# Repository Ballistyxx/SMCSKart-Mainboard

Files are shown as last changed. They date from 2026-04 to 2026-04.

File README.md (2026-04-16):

# SMCSKart Mainboard

Custom PCB integrating every system in the SMCS Robotics 8th period go-kart. The board acts as the central hub between a Raspberry Pi 4, a Teensy 4.1, all motor controller I/O, sensors, and peripherals.

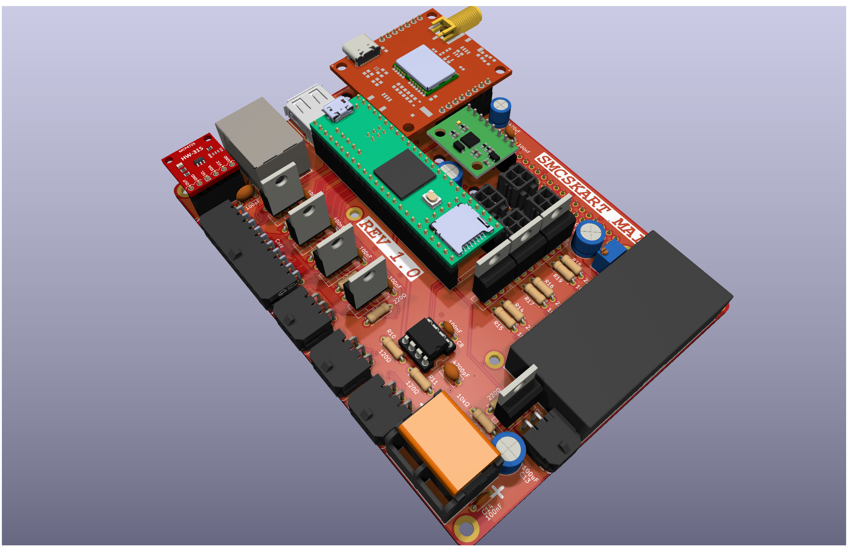
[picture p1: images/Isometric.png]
Isometric View of the SMCSKart PCB


<div style="display: flex; justify-content: space-between;">
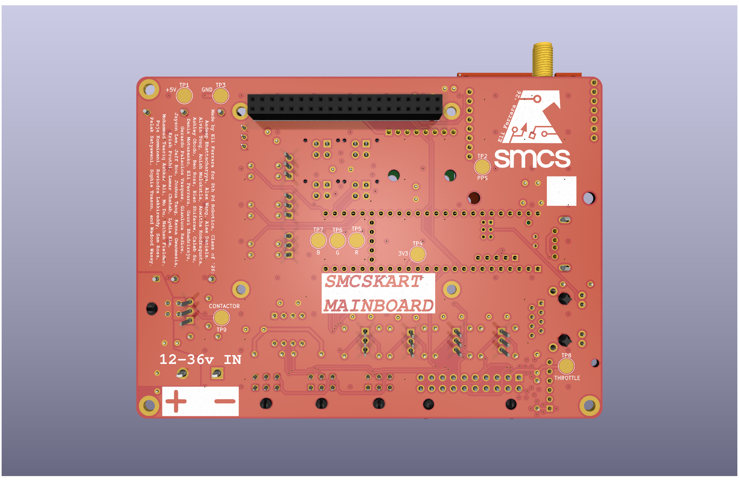
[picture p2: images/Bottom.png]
  
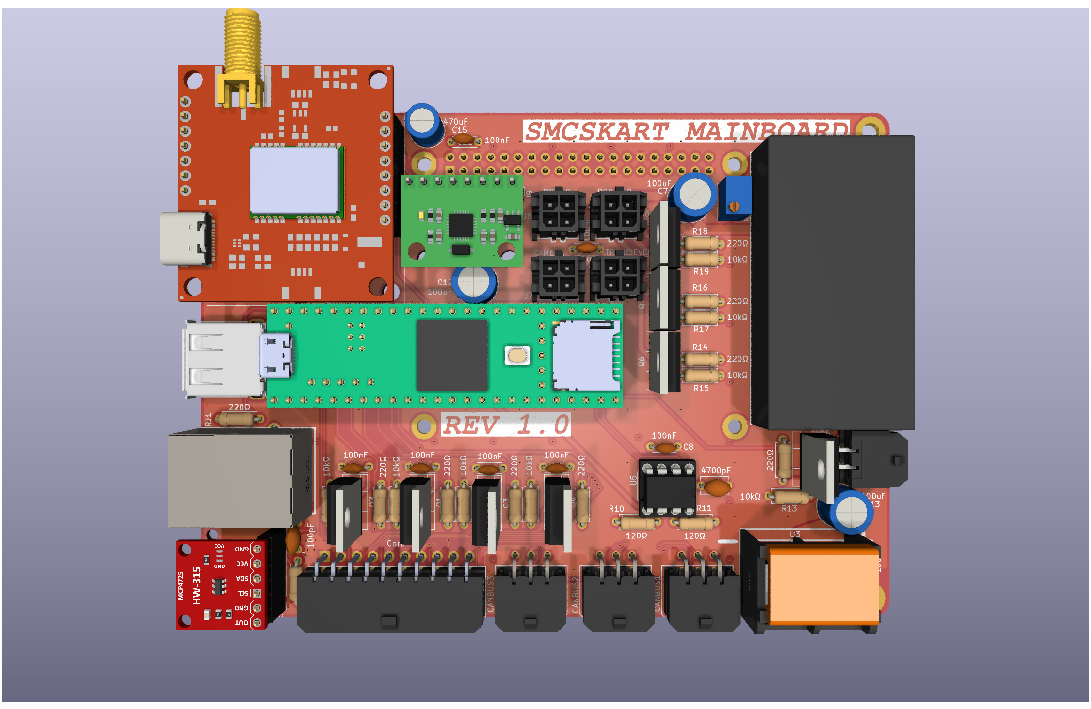
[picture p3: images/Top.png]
  
</div>

---

## Components

| Component | Description |
|---|---|
| Raspberry Pi 4 | Main compute; connected via 40-pin header |
| Teensy 4.1 | Real-time microcontroller with onboard Ethernet |
| NEO-M9N | GPS module (connected to Pi I2C + PPS to Teensy) |
| MPU6050 | 6-axis accelerometer/gyroscope (connected to Pi I2C) |
| MCP4725 | 12-bit DAC for throttle signal generation (connected to Teensy I2C) |
| MCP2562-E/P | CAN bus transceiver |
| IRLZ44N | Logic-level N-channel MOSFETs for all toggle/switch outputs (with pulldown resistors) |
| ND721000 | FarDriver BLDC/PMSM speed controller (RS232 interface) |

---

## Power Rails

The board supplies three voltage rails available on the extra power port:

| Rail | Voltage |
|---|---|
| 3V3 | 3.3 V |
| 5V | 5 V |
| 24V | 24 V (also used for LED strip) |

---

## Teensy 4.1 Pin Assignments

### Serial / UART

| Pin(s) | Interface | Connected To | Notes |
|---|---|---|---|
| 0, 1 | Serial1 (TX, RX) | ND721000 ESC | RS232 level — programming/telemetry port on ESC |
| 7, 8 | Serial2 (TX, RX) | Raspberry Pi 4 | UART bridge between Teensy and Pi |
| 14, 15 | Serial3 (TX, RX) | Transceiver module | RF/wireless transceiver comms |
| 34, 35 | Serial8 (TX, RX) | FPV camera | UART control for FPV camera |

### I2C

| Pin(s) | Bus | Connected To |
|---|-----|---|
| 18, 19 | SDA, SCL | MCP4725 DAC (throttle control) |

### CAN Bus

| Pin(s) | Signal | Notes |
|---|---|---|
| 30, 31 | CRX, CTX | Via MCP2562-E/P transceiver; 120 Ω termination required at each end |

### Digital I/O — ESC Control & Sensors

All toggle output pins drive an IRLZ44N MOSFET with a pulldown resistor, providing an active-low ground signal to the ESC connector.

| Pin | Function | ESC Signal | Direction |
|-----|---|---|---|
| 2 | Hall Pulses input | Hall Pulses (ESC pin 18) | Input from ESC |
| 3 | Reverse toggle | REV (ESC pin 8) | Output to ESC |
| 4 | Brake toggle | Low Brake (ESC pin 21) | Output to ESC |
| 5 | High speed toggle | High Speed (ESC pin 3) | Output to ESC |
| 6 | Low speed toggle | Low Speed (ESC pin 2) | Output to ESC |
| 9 | Cruise control | Cruise/Boost connector | Output to ESC |
| 10 | PPS | NEO-M9N GPS pulse-per-second | Input from GPS |
| 32 | Contactor toggle | Main contactor relay | Output |

### PWM — LED Strip (24 V)

| Pin | Channel |
|-----|---|
| 37 | Red |
| 36 | Green |
| 33 | Blue |

### Auxiliary (EX1–EX5)

| Pin | Label |
|-----|---|
| 25 | EX1 |
| 26 | EX2 |
| 27 | EX3 |
| 28 | EX4 |
| 29 | EX5 |

---

## Raspberry Pi 4 I2C Bus

| Device | Address | Function |
|---|---|---|
| NEO-M9N | — | GPS module |
| MPU6050 | 0x68 | Accelerometer / Gyroscope |

---

## ND721000 ESC Interface

The Teensy communicates with the ND721000 over **Serial1 (pins 0/1) at RS232 levels** (programming/telemetry port). In addition, discrete signals are routed between the board and the ESC's connector harness.

### ESC Connector Pin Reference

| ESC Pin | Color | Signal | Direction | Teensy Pin | Notes |
|---|---|---|---|---|---|
| 1 | Yellow | Hall A | → ESC | — | Motor hall sensor A |
| 2 | Blue-White | Low Speed | ← Teensy | 6 | Ground to activate low speed profile |
| 3 | Yellow-White | High Speed | ← Teensy | 5 | Ground to activate high speed profile |
| 4 | Red | HALL+ | — | — | ~14 V supply to hall sensors / encoder |
| 5 | Brown-Yellow | CAN L | ↔ | — | CAN bus low (optional; 120 Ω termination required) |
| 6 | Black | GND (Hall) | — | — | Hall sensor ground |
| 7 | Black | B− / GND | — | — | Battery negative / signal ground |
| 8 | Brown-White | REV | ← Teensy | 3 | Ground to request reverse direction |
| 9 | Purple | Speedometer signal | → | — | Analog speed output for speedometer gauge |
| 10 | Orange | Key | — | — | Main power-on input (connect to key switch via 5A fuse) |
| 11 | Gray | High Brake | ← Teensy | 4 | Active-high (12 V) brake input |
| 12 | Green | Hall B | → ESC | — | Motor hall sensor B |
| 13 | Light-Blue | SPD (digital speed pulse) | → | — | Square-wave RPM output for digital speedo / ECU |
| 14 | Black-White | FW (anti-theft) | ← | — | Ground to activate anti-theft lockout (error code 6) |
| 15 | Red-Yellow | CAN H | ↔ | — | CAN bus high (optional; 120 Ω termination required) |
| 16 | Black | GND (serial/switch) | — | — | Signal ground for serial and switch circuits |
| 17 | White | Hall P (encoder index) | → ESC | — | Once-per-revolution encoder reference pulse |
| 18 | Brown | Hall Pulses signal | → Teensy | 2 | Speed pulse output used as tachometer reference |
| 19 | Brown-Red | Lock Phase | — | — | Anti-theft motor phase lock wire |
| 20 | Orange | Key (anti-theft) | — | — | Secondary key input for anti-theft subsystem |
| 21 | Yellow-Green | Low Brake | ← Teensy | 4 | Active-low brake input; ground to signal braking |
| 22 | Blue | Hall C | → ESC | — | Motor hall sensor C |
| 23 | Brown-Blue | TxD (serial) | → Teensy | 0 (RX) | ESC serial transmit → Teensy Serial1 RX |
| 24 | White | Motor Temp | → ESC | — | Motor temperature sensor (PTC/NTC/KTY) |
| 25 | — | — | — | — | — |
| 26 | Black | GND (throttle/brake) | — | — | Shared signal ground for throttle and brake circuits |
| 27 | Green-White | TPS (throttle) | ← DAC | — | Throttle position signal (0.5–4.3 V); driven by MCP4725 |
| 28 | Red-White | ACC+ (5 V) | → throttle sensor | — | 5 V regulated supply for throttle sensor |
| 29 | Brown-Green | V+ (serial power) | → adapter | — | 5 V supply for USB-TTL programming adapter |
| 30 | Pink | B+ (anti-theft) | — | — | Always-live battery positive for anti-theft device |
| 31 | Brown-Red | RxD (serial) | ← Teensy | 1 (TX) | ESC serial receive ← Teensy Serial1 TX |

> **Note:** High Brake (pin 11) is active-high (12 V) while Low Brake (pin 21) is active-low (GND). Both can signal braking; the board uses pin 21 via MOSFET toggle (Teensy pin 4).
> **Note:** Medium speed mode is the ESC default when neither High Speed nor Low Speed is grounded.

---

## External Connectors / Ports

| Port | Description |
|---|---|
| 40-pin header | Raspberry Pi 4 HAT connector |
| USB-A | HID peripheral (keyboard, gamepad, etc.) |
| Ethernet | Networking (Teensy 4.1 native Ethernet) |
| CAN × 3 | CANBUS + I2C interface ports |
| Contactor | Trigger port for main contactor relay (Teensy pin 32) |
| FPV camera | UART port (Teensy Serial8, pins 34/35) |
| Transceiver | RF transceiver UART port (Teensy Serial3, pins 14/15) |
| Power port | Extra 3V3 / 5V / 24V supply breakout |
| LED strip | 24 V RGB PWM output (pins 37, 36, 33) |

For images of each port's annotated pinout, see [./docs/PINOUTS.md](./docs/PINOUTS.md)

Made by Eli Ferrara, SMCS Class of 2026
MIT License

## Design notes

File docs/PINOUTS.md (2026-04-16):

# GPIO Pinouts

<div align="center">
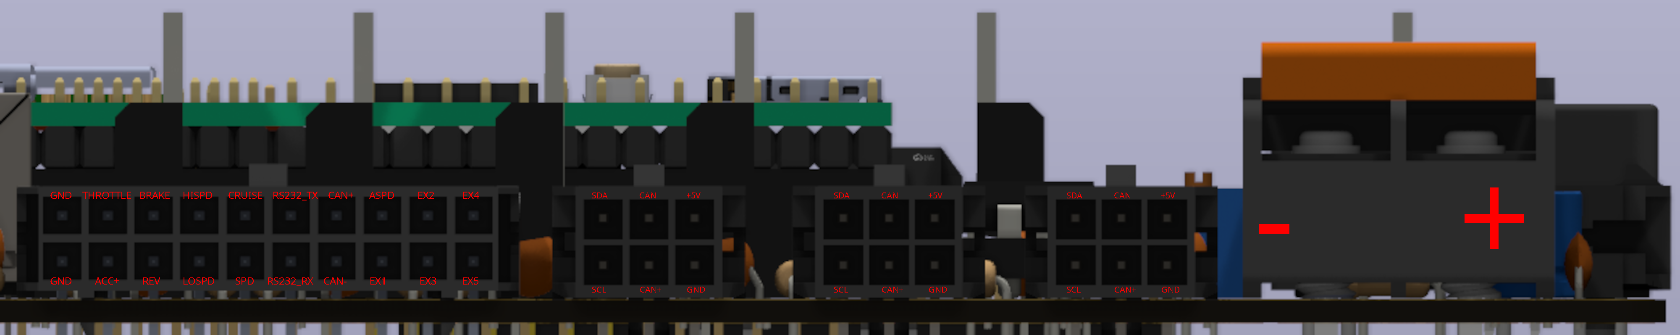
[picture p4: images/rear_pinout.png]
Rear Pinout
  
  <p><i>Rear view pinout diagram</i></p>
</div>

<div align="center">
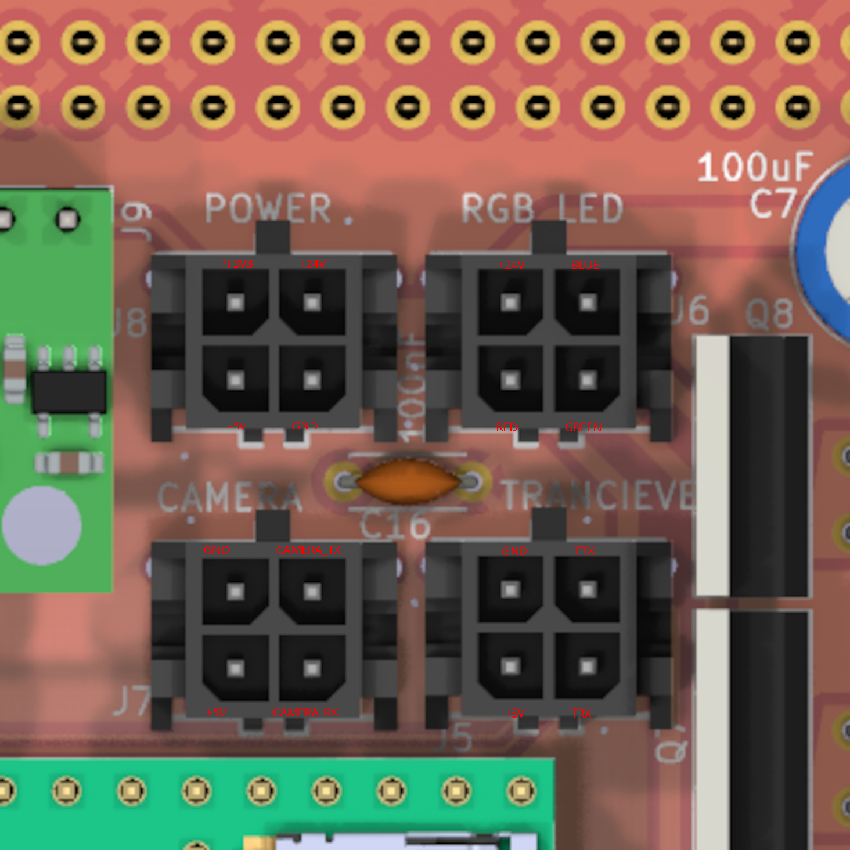
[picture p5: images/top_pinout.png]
Top Pinout
  
  <p><i>Top view pinout diagram; NOTE: TTX and TRX correspond to the tranciever's TX and RX, not the Teensy's TX and RX. Likewise, CAMERA_TX and CAMERA_RX correspond to the camera's TX and RX.</i></p>
</div>

<div align="center">
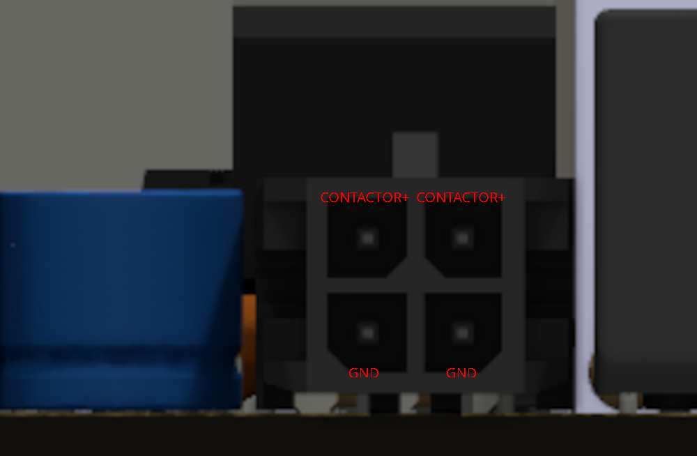
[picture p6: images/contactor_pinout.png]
Contactor Pinout
  
  <p><i>Contactor pinout diagram</i></p>
</div>

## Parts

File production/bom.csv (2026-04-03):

Designator | Footprint | Quantity | Value | LCSC Part #
C1, C10, C11, C14, C16, C3, C4, C5, C8 | C_Disc_D4.3mm_W1.9mm_P5.00mm | 9 | 100nF
C12, C13, C7, C9 | C_Radial_D8.0mm_H7.0mm_P3.50mm | 4 | 100uF
C15 | C_Radial_D6.3mm_H7.0mm_P2.50mm | 1 | 470uF
C2 | C_Disc_D6.0mm_W2.5mm_P5.00mm | 1 | 100pF
C6 | C_Disc_D5.1mm_W3.2mm_P5.00mm | 1 | 4700pF
CANBUS1, CANBUS2, CANBUS3 | Molex_Micro-Fit_3.0_43045-0600_2x03_P3.00mm_Horizontal | 3 | ZX-MX3_0-2-3PWZ | C7541602
J1 | PinSocket_2x20_P2.54mm_Vertical | 1 | Raspberry_Pi_4
J2 | CONN-TH_20P-P3.00_HC-MX3.0-2X10AW | 1 | Core
J3 | PinHeader_1x06_P2.54mm_Vertical | 1 | MCP4275_Breakout
J4 | CONN-TH_0430450400 | 1 | 0430450400 | C122413
J5 | CONN-TH_4P-P3.00_HC-MX3.0-2X2A | 1 | TRANCIEVER | C7541613
J6 | CONN-TH_4P-P3.00_HC-MX3.0-2X2A | 1 | RGB_LED | C7541613
J7 | CONN-TH_4P-P3.00_HC-MX3.0-2X2A | 1 | CAMERA | C7541613
J8 | CONN-TH_4P-P3.00_HC-MX3.0-2X2A | 1 | POWER | C7541613
J9 | PinHeader_1x08_P2.54mm_Vertical | 1 | MPU-6050_Breakout
Q1, Q2, Q3, Q4, Q5, Q6, Q7, Q8 | TO-220-3_Vertical | 8 | IRLZ44N
R1, R13, R15, R17, R19, R5, R8, R9 | R_Axial_DIN0207_L6.3mm_D2.5mm_P7.62mm_Horizontal | 8 | 10kΩ
R10, R11 | R_Axial_DIN0207_L6.3mm_D2.5mm_P7.62mm_Horizontal | 2 | 120Ω
R12, R14, R16, R18, R2, R20, R4, R6, R7 | R_Axial_DIN0207_L6.3mm_D2.5mm_P7.62mm_Horizontal | 9 | 220Ω
R3 | R_Axial_DIN0207_L6.3mm_D2.5mm_P7.62mm_Horizontal | 1 | 1kΩ
RJ1 | RJ45-TH_HR913550A | 1 | HR913550A | C163507
RV1 | Potentiometer_Bourns_3266Y_Vertical | 1 | R_Potentiometer
SPARKFUN-GPS-1 | Sparkfun-NEO-M9N-Breakout-Board | 1 | ~
TP1 | TestPoint_Pad_D4.0mm | 1 | +5V
TP2 | TestPoint_Pad_D4.0mm | 1 | PPS
TP3 | TestPoint_Pad_D4.0mm | 1 | GND
TP4 | TestPoint_Pad_D4.0mm | 1 | 3V3
TP5 | TestPoint_Pad_D4.0mm | 1 | R
TP6 | TestPoint_Pad_D4.0mm | 1 | G
TP7 | TestPoint_Pad_D4.0mm | 1 | B
TP8 | TestPoint_Pad_D4.0mm | 1 | THROTTLE
TP9 | TestPoint_Pad_D4.0mm | 1 | CONTACTOR
U1 | Teensy41 | 1 | Teensy4.1
U2 | PWRM-TH_TURBXXXXLD-30WR3 | 1 | URB4805LD-30WR3_C20199272 | C20199272
U3 | CONN-TH_HB9500M-9.5-2P | 1 | HB9500M-9_5-2P | C601239
U5 | DIP-8_W7.62mm | 1 | MCP2562-E-P
USB1 | USB-A-TH_USB-302-T | 1 | USB-302 | C112456

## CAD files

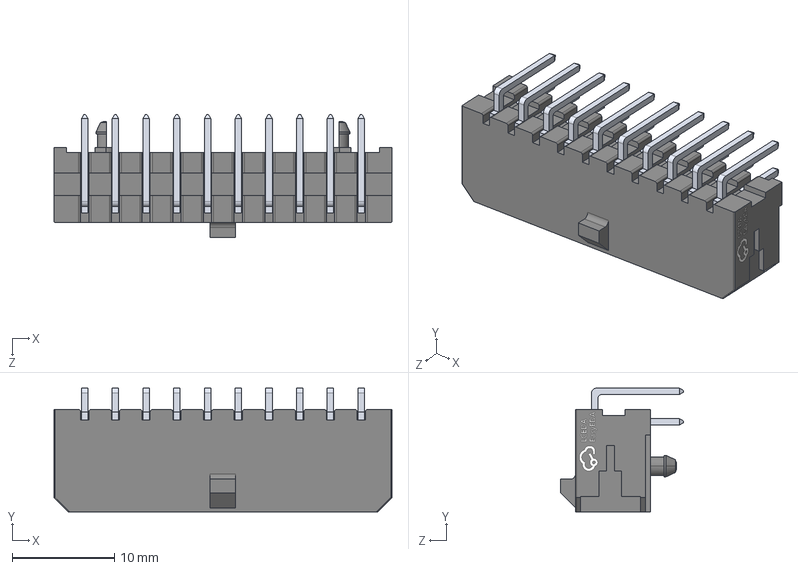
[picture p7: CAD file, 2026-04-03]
jlcpcb_lib/3dmodels/CONN-TH_20P-P3.00_HC-MX3.0-2X10AW.step
33.0 x 12.1 x 12.0 mm

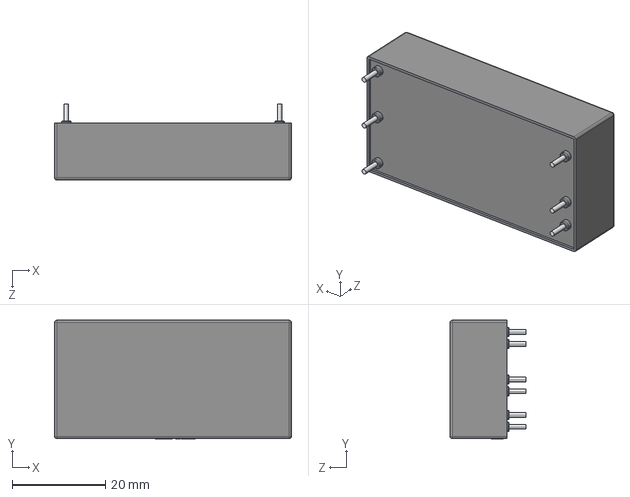
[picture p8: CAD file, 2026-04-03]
jlcpcb_lib/3dmodels/PWRM-TH_TURBXXXXLD-30WR3.step
50.8 x 25.4 x 16.3 mm

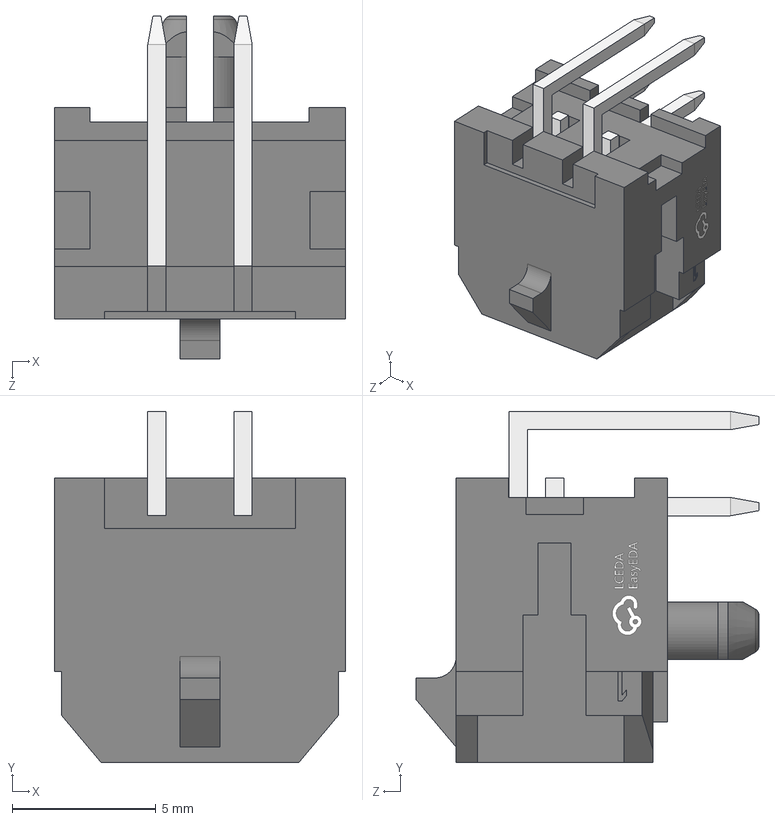
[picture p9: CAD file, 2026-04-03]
jlcpcb_lib/3dmodels/CONN-TH_0430450400.step
10.2 x 12.2 x 11.9 mm

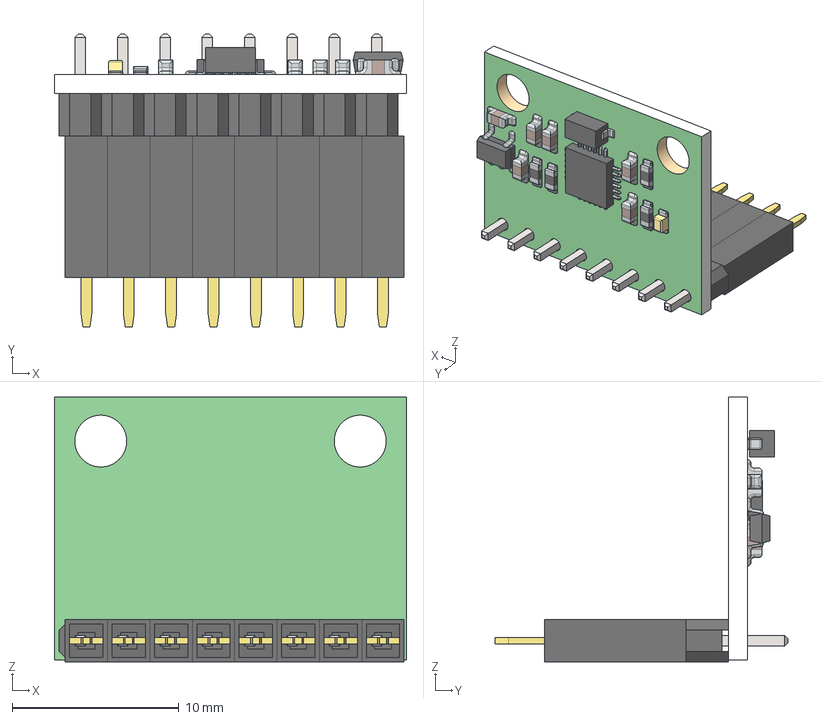
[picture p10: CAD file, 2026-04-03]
jlcpcb_lib/3dmodels/MPU-6050-on-female-header.step
21.1 x 17.6 x 15.9 mm
Base
pin header x 8
sensor chip
S2NH chip
Resistor small x 6
Resistor small black x 4
Small LED
Resistor black
SIL_Socket_Body x 8
SIL_SocketPin x 8

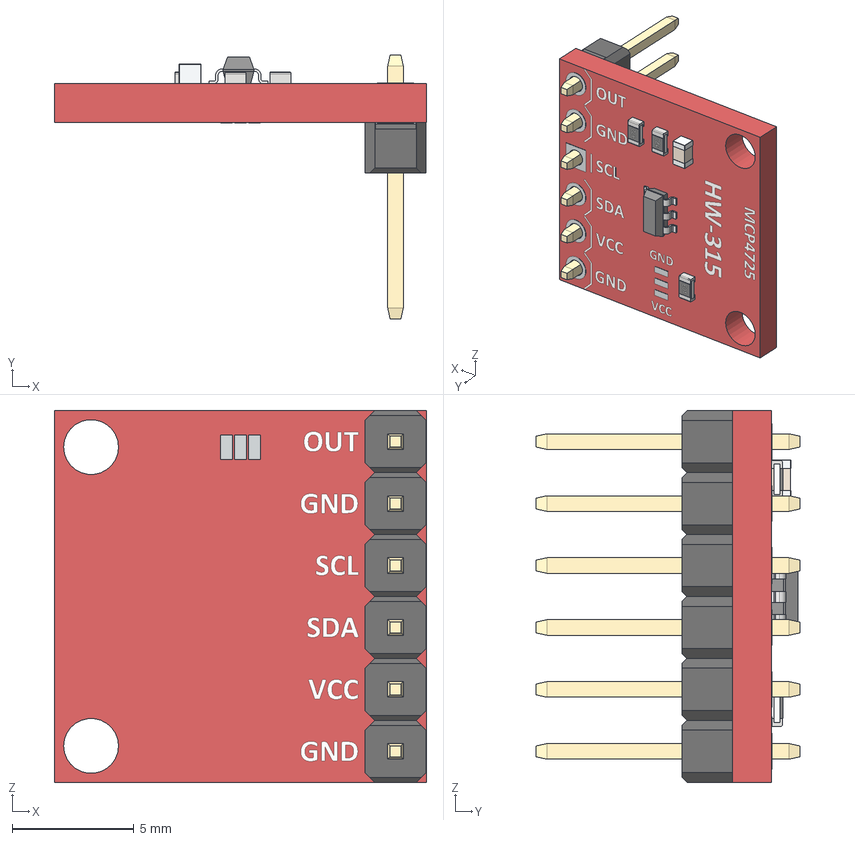
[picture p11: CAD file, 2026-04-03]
jlcpcb_lib/3dmodels/MCP4275-Header.step
15.2 x 10.8 x 15.2 mm
1x1 Male Pin Header x 12
R472_0603_1 x 4
R103_0603 x 4
C0603 x 3
R472_0603 x 4
SOT23-6
PCB

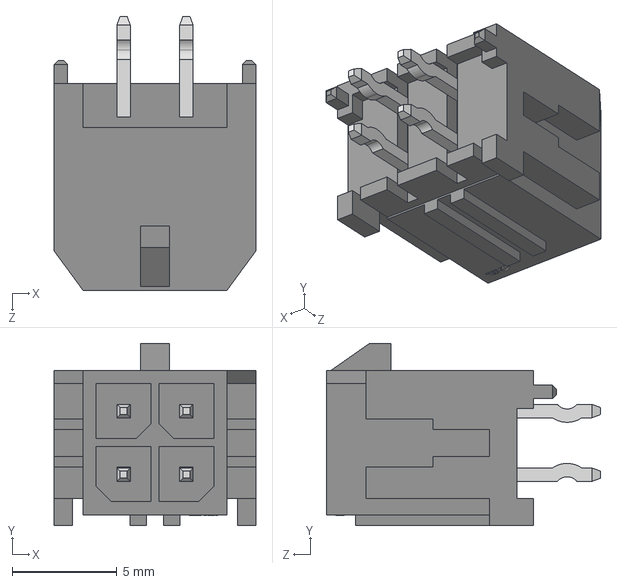
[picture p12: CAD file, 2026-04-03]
jlcpcb_lib/3dmodels/CONN-TH_4P-P3.00_HC-MX3.0-2X2A.step
9.65 x 8.70 x 13.1 mm

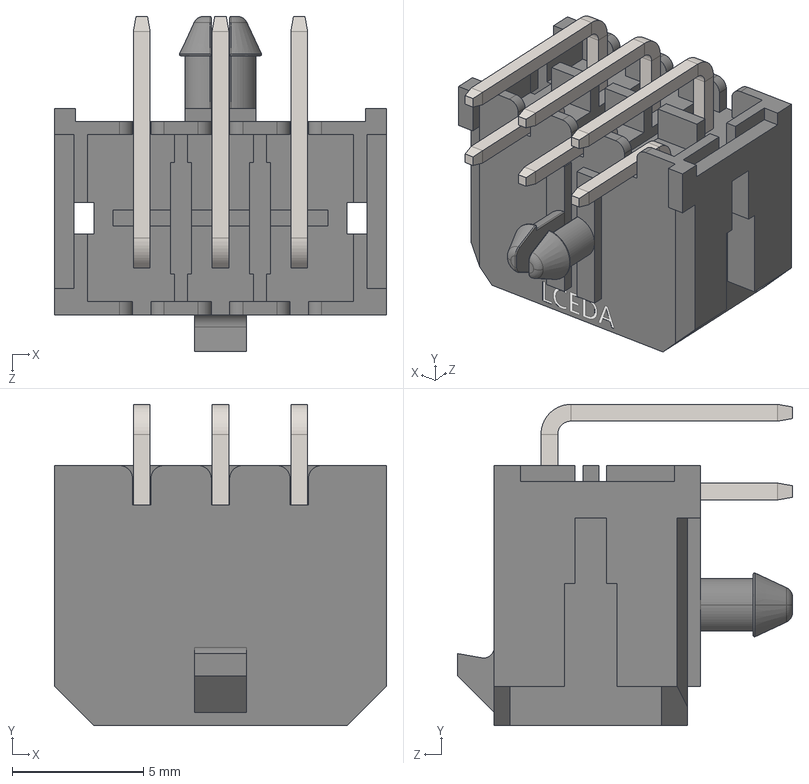
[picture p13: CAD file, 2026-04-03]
jlcpcb_lib/3dmodels/CONN-TH_43045-0600.step
12.7 x 12.2 x 12.8 mm

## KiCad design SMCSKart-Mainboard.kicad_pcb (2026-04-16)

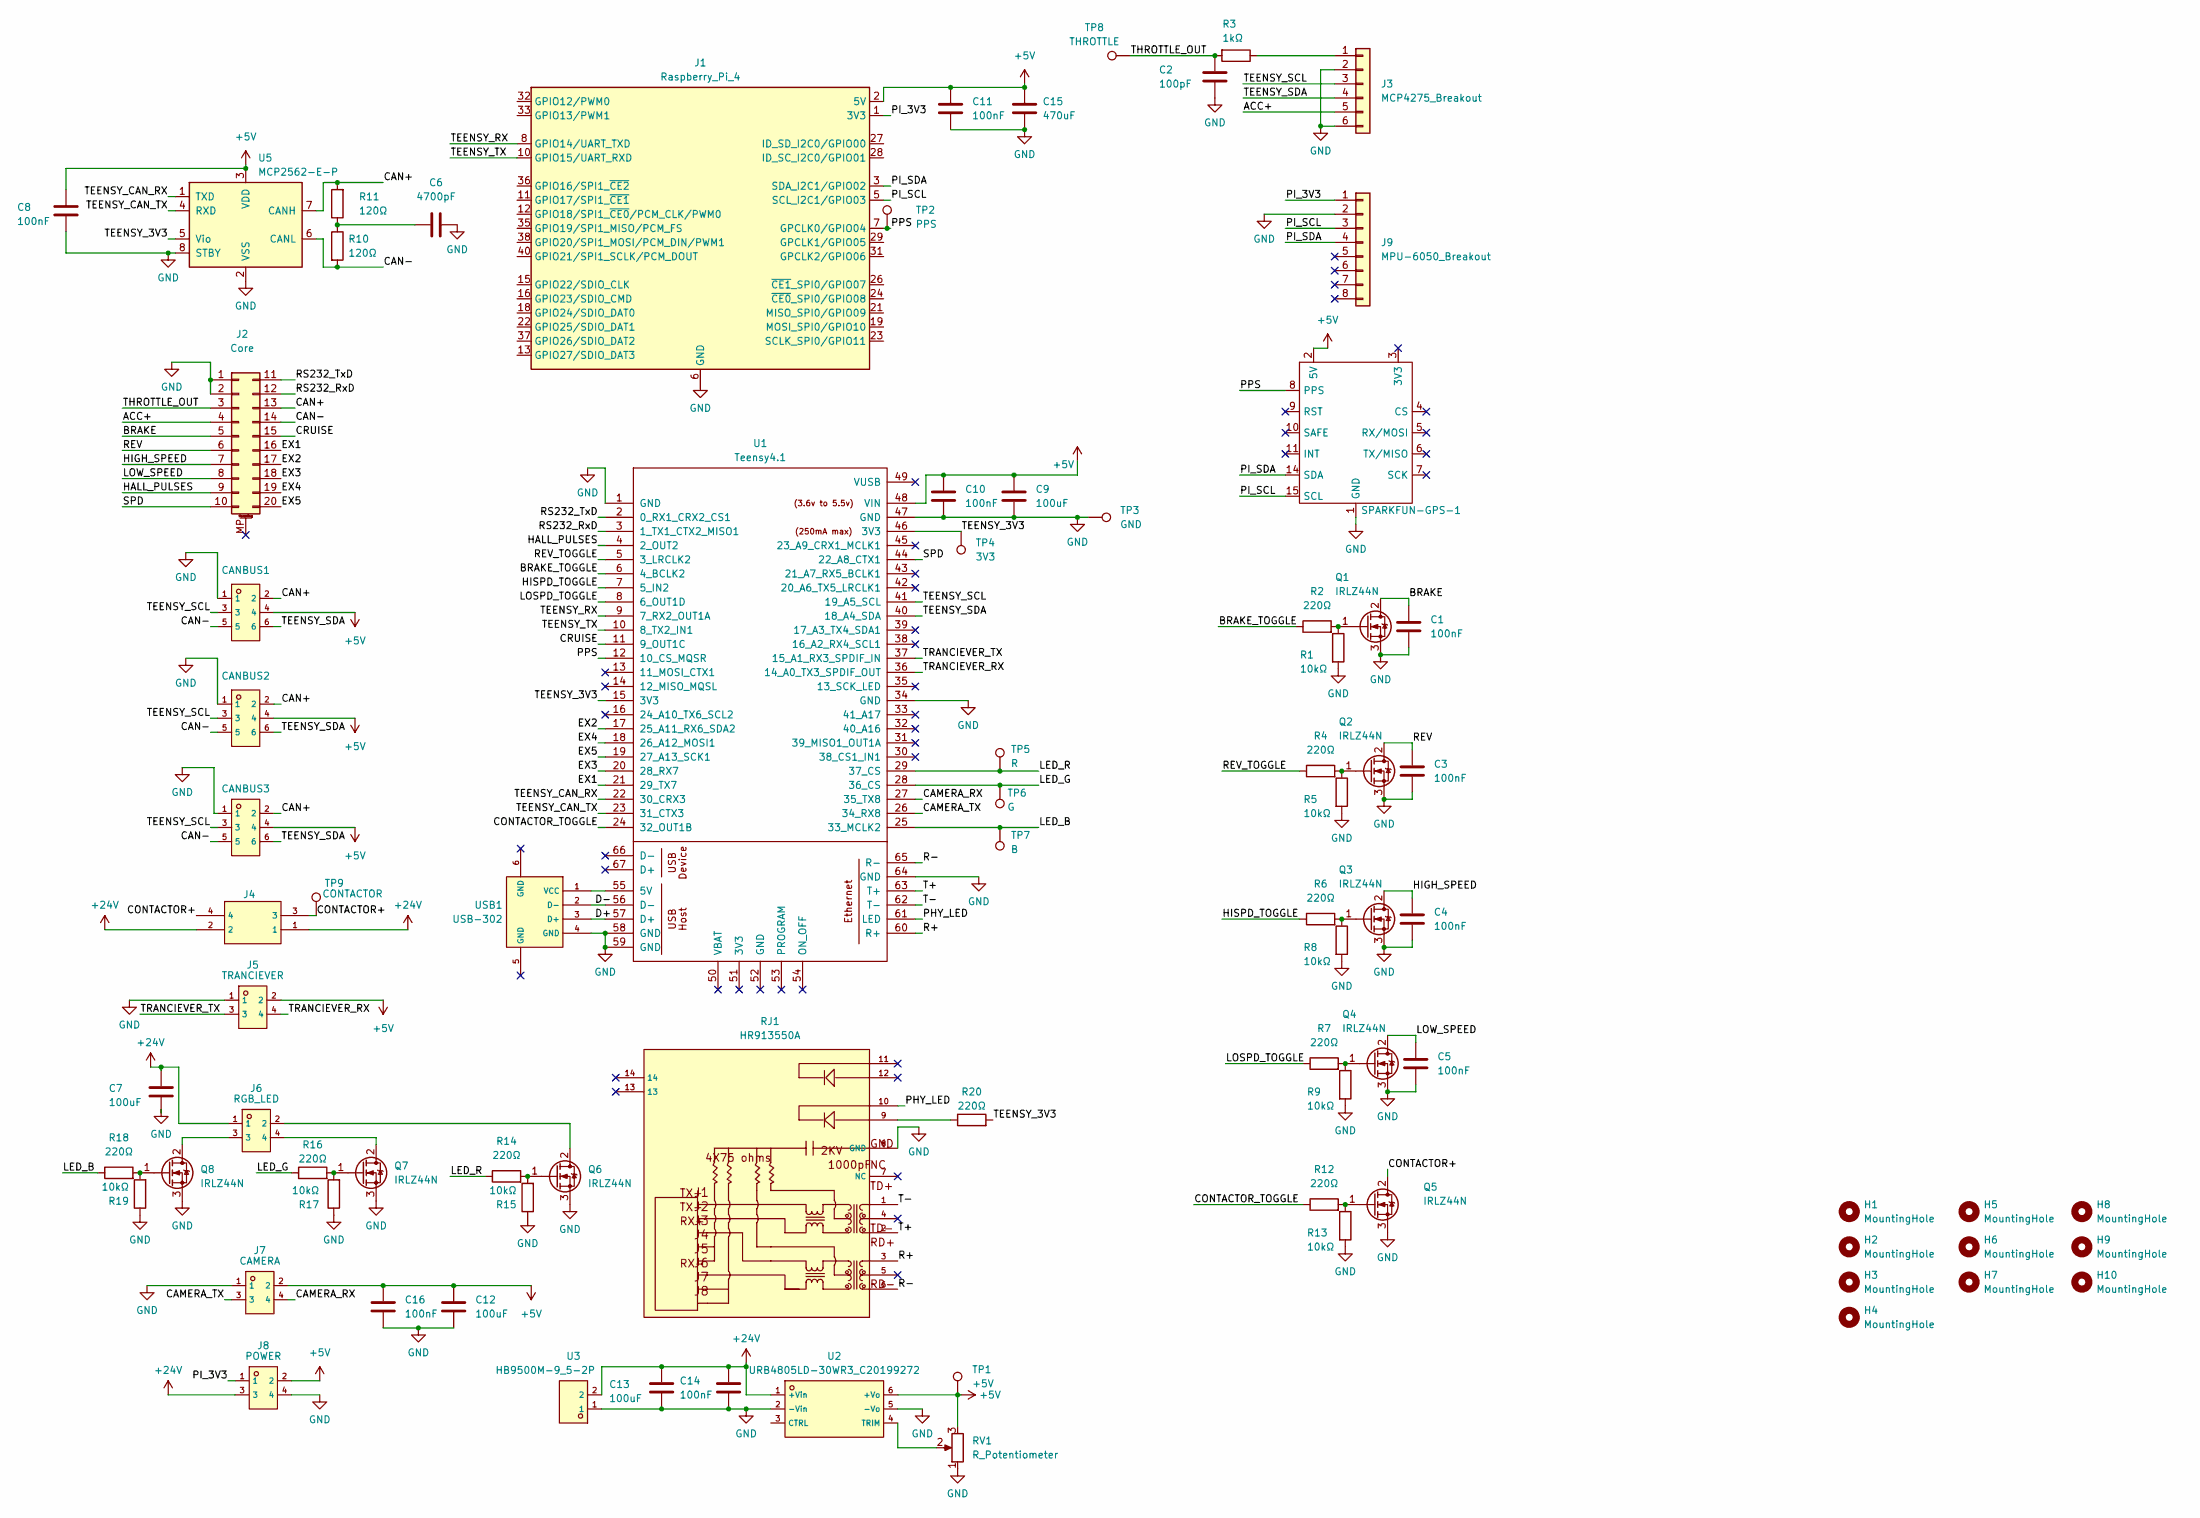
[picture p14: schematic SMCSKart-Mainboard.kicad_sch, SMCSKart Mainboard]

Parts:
C1, C3, C4, C5, C8, C10, C11, C14, C16: 100nF; C_Disc_D4.3mm_W1.9mm_P5.00mm
C2: 100pF; C_Disc_D6.0mm_W2.5mm_P5.00mm
C6: 4700pF; C_Disc_D5.1mm_W3.2mm_P5.00mm
C7, C9, C12, C13: 100uF; C_Radial_D8.0mm_H7.0mm_P3.50mm
C15: 470uF; C_Radial_D6.3mm_H7.0mm_P2.50mm
CANBUS1, CANBUS2, CANBUS3: ZX-MX3_0-2-3PWZ; Molex_Micro-Fit_3.0_43045-0600_2x03_P3.00mm_Horizontal; LCSC C7541602
H1, H2, H3, H4: MountingHole; MountingHole_2.7mm_M2.5_DIN965_Pad
H5, H6, H7: MountingHole; MountingHole_3.2mm_M3_DIN965_Pad
H8, H9: MountingHole; MountingHole_3.2mm_M3
H10: MountingHole; MountingHole_2.2mm_M2_DIN965
J1: Raspberry_Pi_4; PinSocket_2x20_P2.54mm_Vertical
J2: Core; CONN-TH_20P-P3.00_HC-MX3.0-2X10AW
J3: MCP4275_Breakout; PinHeader_1x06_P2.54mm_Vertical
J4: 0430450400; CONN-TH_0430450400; LCSC C122413
J5: TRANCIEVER; CONN-TH_4P-P3.00_HC-MX3.0-2X2A; LCSC C7541613
J6: RGB_LED; CONN-TH_4P-P3.00_HC-MX3.0-2X2A; LCSC C7541613
J7: CAMERA; CONN-TH_4P-P3.00_HC-MX3.0-2X2A; LCSC C7541613
J8: POWER; CONN-TH_4P-P3.00_HC-MX3.0-2X2A; LCSC C7541613
J9: MPU-6050_Breakout; PinHeader_1x08_P2.54mm_Vertical
Q1, Q2, Q3, Q4, Q5, Q6, Q7, Q8: IRLZ44N; TO-220-3_Vertical
R1, R5, R8, R9, R13, R15, R17, R19: 10kΩ; R_Axial_DIN0207_L6.3mm_D2.5mm_P7.62mm_Horizontal
R2, R4, R6, R7, R12, R14, R16, R18, R20: 220Ω; R_Axial_DIN0207_L6.3mm_D2.5mm_P7.62mm_Horizontal
R3: 1kΩ; R_Axial_DIN0207_L6.3mm_D2.5mm_P7.62mm_Horizontal
R10, R11: 120Ω; R_Axial_DIN0207_L6.3mm_D2.5mm_P7.62mm_Horizontal
RJ1: HR913550A; RJ45-TH_HR913550A; LCSC C163507
RV1: R_Potentiometer; Potentiometer_Bourns_3266Y_Vertical
SPARKFUN-GPS-1: Sparkfun-NEO-M9N-Breakout-Board
TP1: +5V; TestPoint_Pad_D4.0mm
TP2: PPS; TestPoint_Pad_D4.0mm
TP3: GND; TestPoint_Pad_D4.0mm
TP4: 3V3; TestPoint_Pad_D4.0mm
TP5: R; TestPoint_Pad_D4.0mm
TP6: G; TestPoint_Pad_D4.0mm
TP7: B; TestPoint_Pad_D4.0mm
TP8: THROTTLE; TestPoint_Pad_D4.0mm
TP9: CONTACTOR; TestPoint_Pad_D4.0mm
U1: Teensy4.1; Teensy41
U2: URB4805LD-30WR3_C20199272; PWRM-TH_TURBXXXXLD-30WR3; LCSC C20199272
U3: HB9500M-9_5-2P; CONN-TH_HB9500M-9.5-2P; LCSC C601239
U5: MCP2562-E-P; DIP-8_W7.62mm
USB1: USB-302; USB-A-TH_USB-302-T; LCSC C112456

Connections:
+5V: C8.1, C9.1, C10.1, C11.1, C12.1, C15.1, C16.1, CANBUS1.4, CANBUS2.4, CANBUS3.4, J1.2 (5V), J1.4 (5V), J5.2, J7.2, J8.2, RV1.3, SPARKFUN-GPS-1.2 (5V), TP1.1, U1.48 (VIN), U2.6 (+Vo), U5.3 (VDD)
+24V: C7.1, C13.1, C14.1, J4.1, J4.2, J6.1, J8.3, U2.1 (+Vin), U3.2
/ACC+: J2.4, J3.5
/BRAKE: C1.1, J2.5, Q1.2 (D)
/BRAKE_TOGGLE: R2.1, U1.6 (4_BCLK2)
/CAMERA_RX: J7.4, U1.27 (35_TX8)
/CAMERA_TX: J7.3, U1.26 (34_RX8)
/CAN+: CANBUS1.2, CANBUS2.2, CANBUS3.2, J2.13, R11.2, U5.7 (CANH)
/CAN-: CANBUS1.5, CANBUS2.5, CANBUS3.5, J2.14, R10.2, U5.6 (CANL)
/CONTACTOR+: J4.3, J4.4, Q5.2 (D), TP9.1
/CONTACTOR_TOGGLE: R12.1, U1.24 (32_OUT1B)
/CRUISE: J2.15, U1.11 (9_OUT1C)
/D+: U1.57 (D+), USB1.3 (D+)
/D-: U1.56 (D-), USB1.2 (D-)
/EX1: J2.16, U1.21 (29_TX7)
/EX2: J2.17, U1.17 (25_A11_RX6_SDA2)
/EX3: J2.18, U1.20 (28_RX7)
/EX4: J2.19, U1.18 (26_A12_MOSI1)
/EX5: J2.20, U1.19 (27_A13_SCK1)
/HALL_PULSES: J2.9, U1.4 (2_OUT2)
/HIGH_SPEED: C4.1, J2.7, Q3.2 (D)
/HISPD_TOGGLE: R6.1, U1.7 (5_IN2)
/LED_B: R18.1, TP7.1, U1.25 (33_MCLK2)
/LED_G: R16.1, TP6.1, U1.28 (36_CS)
/LED_R: R14.1, TP5.1, U1.29 (37_CS)
/LOSPD_TOGGLE: R7.1, U1.8 (6_OUT1D)
/LOW_SPEED: C5.1, J2.8, Q4.2 (D)
/PHY_LED: RJ1.10, U1.61 (LED)
/PI_3V3: J1.1 (3V3), J1.17 (3V3), J8.1, J9.1
/PI_SCL: J1.5 (SCL_I2C1/GPIO03), J9.3, SPARKFUN-GPS-1.15 (SCL)
/PI_SDA: J1.3 (SDA_I2C1/GPIO02), J9.4, SPARKFUN-GPS-1.14 (SDA)
/PPS: J1.7 (GPCLK0/GPIO04), SPARKFUN-GPS-1.8 (PPS), TP2.1, U1.12 (10_CS_MQSR)
/R+: RJ1.3, U1.60 (R+)
/R-: RJ1.6, U1.65 (R-)
/REV: C3.1, J2.6, Q2.2 (D)
/REV_TOGGLE: R4.1, U1.5 (3_LRCLK2)
/RS232_RxD: J2.12, U1.3 (1_TX1_CTX2_MISO1)
/RS232_TxD: J2.11, U1.2 (0_RX1_CRX2_CS1)
/SPD: J2.10, U1.44 (22_A8_CTX1)
/T+: RJ1.2, U1.63 (T+)
/T-: RJ1.1, U1.62 (T-)
/TEENSY_3V3: R20.2, TP4.1, U1.15 (3V3), U1.46 (3V3), U5.5 (Vio)
/TEENSY_CAN_RX: U1.22 (30_CRX3), U5.1 (TXD)
/TEENSY_CAN_TX: U1.23 (31_CTX3), U5.4 (RXD)
/TEENSY_RX: J1.8 (GPIO14/UART_TXD), U1.9 (7_RX2_OUT1A)
/TEENSY_SCL: CANBUS1.3, CANBUS2.3, CANBUS3.3, J3.3, U1.41 (19_A5_SCL)
/TEENSY_SDA: CANBUS1.6, CANBUS2.6, CANBUS3.6, J3.4, U1.40 (18_A4_SDA)
/TEENSY_TX: J1.10 (GPIO15/UART_RXD), U1.10 (8_TX2_IN1)
/THROTTLE_OUT: C2.1, J2.3, R3.2, TP8.1
/TRANCIEVER_RX: J5.4, U1.36 (14_A0_TX3_SPDIF_OUT)
/TRANCIEVER_TX: J5.3, U1.37 (15_A1_RX3_SPDIF_IN)
GND: C1.2, C2.2, C3.2, C4.2, C5.2, C6.1, C7.2, C8.2, C9.2, C10.2, C11.2, C12.2, C13.2, C14.2, C15.2, C16.2, CANBUS1.1, CANBUS2.1, CANBUS3.1, J1.6 (GND), J1.9 (GND), J1.14 (GND), J1.20 (GND), J1.25 (GND), J1.30 (GND), J1.34 (GND), J1.39 (GND), J2.1, J2.2, J3.2, J3.6, J5.1, J7.1, J8.4, J9.2, Q1.3 (S), Q2.3 (S), Q3.3 (S), Q4.3 (S), Q5.3 (S), Q6.3 (S), Q7.3 (S), Q8.3 (S), R1.2, R5.2, R8.2, R9.2, R13.2, R15.1, R17.1, R19.1, RJ1.8 (GND), RV1.1, SPARKFUN-GPS-1.1 (GND), TP3.1, U1.1 (GND), U1.34 (GND), U1.47 (GND), U1.58 (GND), U1.59 (GND), U1.64 (GND), U2.2 (-Vin), U2.5 (-Vo), U3.1, U5.2 (VSS), U5.8 (STBY), USB1.4 (GND)
unnamed: C6.2, R10.1, R11.1
unnamed: J3.1, R3.1
unnamed: Q1.1 (G), R1.1, R2.2
unnamed: Q2.1 (G), R4.2, R5.1
unnamed: Q3.1 (G), R6.2, R8.1
unnamed: Q4.1 (G), R7.2, R9.1
unnamed: Q5.1 (G), R12.2, R13.1
unnamed: J6.2, Q6.2 (D)
unnamed: Q6.1 (G), R14.2, R15.2
unnamed: J6.4, Q7.2 (D)
unnamed: Q7.1 (G), R16.2, R17.2
unnamed: J6.3, Q8.2 (D)
unnamed: Q8.1 (G), R18.2, R19.2
unnamed: R20.1, RJ1.9
unnamed: U1.55 (5V), USB1.1 (VCC)
unnamed: RV1.2, U2.4 (TRIM)

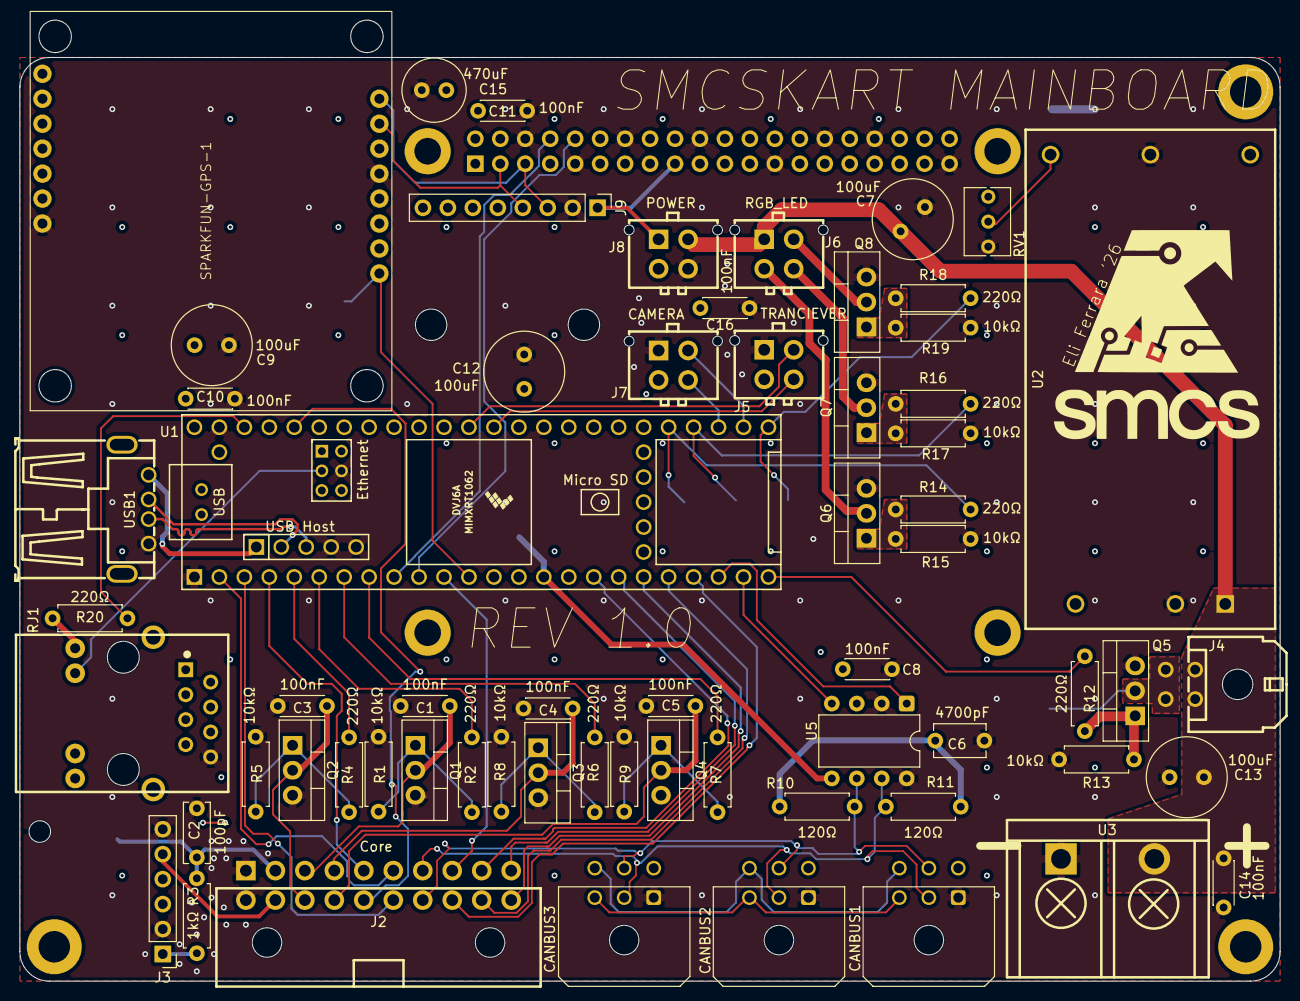
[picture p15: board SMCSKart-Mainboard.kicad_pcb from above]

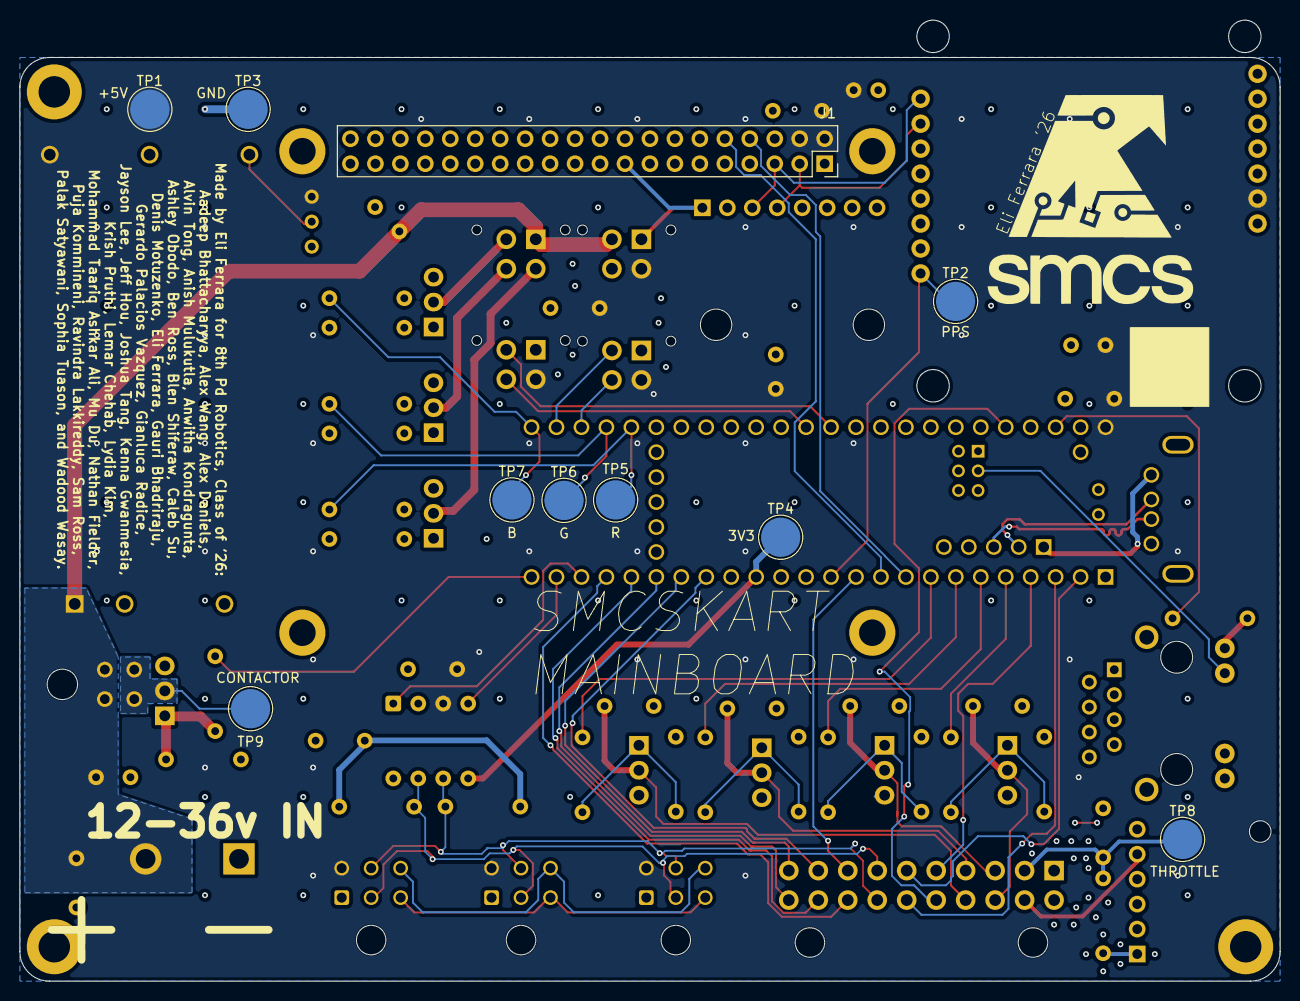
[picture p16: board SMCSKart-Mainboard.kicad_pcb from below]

Board: 4 copper layers, 128.2 x 97.8 mm, 83 parts (10 on the bottom side), 68 nets.

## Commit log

2026-04-16 update kicad + document connector pinouts
    [SMCSKart-Mainboard.kicad_pcb, SMCSKart-Mainboard.kicad_sch]
2026-04-20 update rear pinout to reflect physical wiring
